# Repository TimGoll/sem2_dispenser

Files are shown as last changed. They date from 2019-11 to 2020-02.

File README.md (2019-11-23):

# SEM2 Projekt - Vitamintablettenspender

## Teil 1 - Konzeptionierung

- **Produktplanung**
    - [ ] Marktanalysen
    - [ ] Wettbewerbsanalysen
    - [ ] Thenologieanalyse
    - [x] Patenanalyse

- **Projektplan**
    - [ ] Aufgaben
    - [ ] Dauer, Beginn und Ende der Aufgaben
    - [ ] Abhängigkeiten zwischen Aufgaben
    - [ ] ggf. kritischer Pfad

- **Anforderungsliste**
    - [ ] Anforderungen des Lastenheftes präzisier sowei um sinnvolle Anforderungen und Angaben inkl. Verweis auf Lage im Kano-Diagramm ärgenzt (min 20)
    - [ ] Konsistenzmatrix für mindestens 10 Hauptanforderungen

- **Funktionsstruktur**
    - [ ] Allgemeine kybernetische Black-Box-Darstellung
    - [ ] Hierarchische Funktionsstruktur (mindestens 10 Teilfunktionen)
    - [ ] Funktionsmodell mit Darstellung der (mindestens 10) wichtigsten Funktionen

- **Lösungsprinzipien**
    - [ ] Morphologischer Kasten mit (jeweils mindestens 4) Taillösungsprinzipien (ggf. durch geeignte Lösungsfindungsmethoden) für diese wichtigsten Funktionen
    - [ ] Verträglichkeitsmatrix für die Teilprinzipien
    - [ ] Kennzeichnung von mindestens 3 möglichen Gesamtlösungskombinationen im morphologischen Kasten
    - [ ] Bewertung dieser Gesamtlösungskombination

- **Grobentwurf / technische Prinzipskizze**
    - [ ] Anfertigung einer technischen Prinzipskizze zur Verdeutlichung des Wirkprinzips

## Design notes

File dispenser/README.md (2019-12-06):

# Dispenser Software

## Needed Libraries

1. Adafruit SSD1306
2. Adafruit GFX
3. Adafruit RTClib

## Software

### Registering Button Callbacks

Button callbacks are a neat system to easily design the software to do actions on the press of a button. Since no memberfunctions of a class can be passed as an callable callback pointer, the function has to be static. The class reference is then passed as an argument.

```cpp
this->buttonHandler->addCallback(10, RISING, &callbackTest, this);
```

The above shown example registers a callback function `callbackTest` and also passes the parent scope with `this`. Therefore all functions and variables of the class can be used in the callback.

```cpp
static void Main::callbackTest(Main* self, uint8_t type) {
    // code here
}
```

This shows the structure of the callback function. The `self` parameter has to be the type of the class itself and can be used inthe same way as `this` is normally used. The type is specific to this button callback and defines the type of the button event (RISING, FALLING, HIGH).

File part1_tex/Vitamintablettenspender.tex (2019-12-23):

%Dokumentklasse
\documentclass[a4paper,12pt, headings=small, bibtotoc, numbers=noenddot]{scrreprt} %bibtotoc = bibliography to table of contents, bindet Literaturverzeichnis in Inhaltsverzeichnis ein
\usepackage[left= 2.5cm,right = 2cm, top = 2cm, bottom = 2cm]{geometry} %Seitenränder
\usepackage[onehalfspacing]{setspace} %1,5 Zeilenabstand

% ============= Packages =============

% Dokumentinformationen
\usepackage[
	pdftitle={Titel der Arbeit},
	pdfsubject={Abschlussarbeit},
	pdfauthor={Max Mustermann},
	pdfkeywords={}
	pdftex=true, 
	colorlinks=true,
 	breaklinks=true,
	citecolor=black,
	linkcolor=black,	
	menucolor=black,	
	urlcolor=black,
]{hyperref}

% Standard Packages
\usepackage{libertine}	%Schriftart "Biolinum", Sans Serif
\renewcommand*\familydefault{\sfdefault} %Setzt die Standardschriftart auf Sans Serif
\usepackage[T1]{fontenc}
\usepackage{mathptmx} %Times new roman
\usepackage[utf8]{inputenc}
\usepackage[ngerman]{babel}
\AtBeginDocument{\renewcommand{\chaptername}{}}

\usepackage{rotating}
\usepackage{subfigure}
\usepackage{graphicx}
\graphicspath{{img/}}

\usepackage{multirow}
\usepackage{placeins}

\usepackage{fancyhdr}
\usepackage{lmodern}
\usepackage{color}
\usepackage{transparent}
\usepackage[justification=centering, singlelinecheck=false]{caption} %Damit die Tabellenbeschriftung zentriert steht
\usepackage{nomencl}
\usepackage{tabularx}
\usepackage{longtable}
\usepackage{booktabs}
\usepackage{pdfpages}
\usepackage{acronym}
\usepackage{setspace}

%Schriftgröße von section auf 12pt setzen
\addtokomafont{section}{\normalsize} 
\addtokomafont{chapter}{\large}
%Abbildungsbeschriftungen fett gedruckt einstellen
\addtokomafont{captionlabel}{\bfseries}

%Abstände zwischen Text und Überschriften
%Zeilenabstände bei Unterkapiteln
\RedeclareSectionCommand[beforeskip=18pt, afterskip=6pt]{section}
%Zeilenabstände bei Unter-unterkapiteln 
\RedeclareSectionCommand[beforeskip=12pt,afterskip=1pt]{subsection}
\RedeclareSectionCommand[%
  beforeskip=0pt,
  afterskip=1\baselineskip plus .1\baselineskip minus .167\baselineskip
]{chapter}

% zusätzliche Schriftzeichen der American Mathematical Society
\usepackage{amsfonts}
\usepackage{amsmath}

\usepackage{float} %erlaubt die Verwendung von H in Bildern
% mu im normalen Text: \textmu
\usepackage{textcomp}

\usepackage[backend=bibtex, style=alphabetic, uniquename=allfull, minalphanames=4, maxalphanames=4]{biblatex}
\addbibresource{Literatur.bib}

% nicht einrücken nach Absatz
\setlength{\parindent}{0pt}

\setcounter{secnumdepth}{4}
\setcounter{tocdepth}{4}

%url umbrechen
\usepackage{url}
\usepackage{microtype} %Sorgt für bessere Platzausnutzung der \hbox bei Umbruechen
\setlength{\emergencystretch}{1em} %Sorgt für bessere Platzausnutzung der \hbox bei Umbruechen

\setcounter{biburlnumpenalty}{100}
\setcounter{biburlucpenalty}{100}
\setcounter{biburllcpenalty}{100}
% ============= Package Einstellungen & Sonstiges ============= 

%römische Aufzählungen mit \RM{Zahl}
\newcommand{\RM}[1]{\MakeUppercase{\romannumeral #1}}

% ============= Dokumentbeginn =============

\begin{document}

\pagestyle{empty}   %leere Seite

%Seitennummerierung neu beginnen, Zahlen [arabic], röm.Zahlen [roman,Roman], Buchstaben [alph,Alph]

%Deckblatt
\label{Coversheet}
\begin{minipage}{0.5\textwidth}
\begin{flushleft}
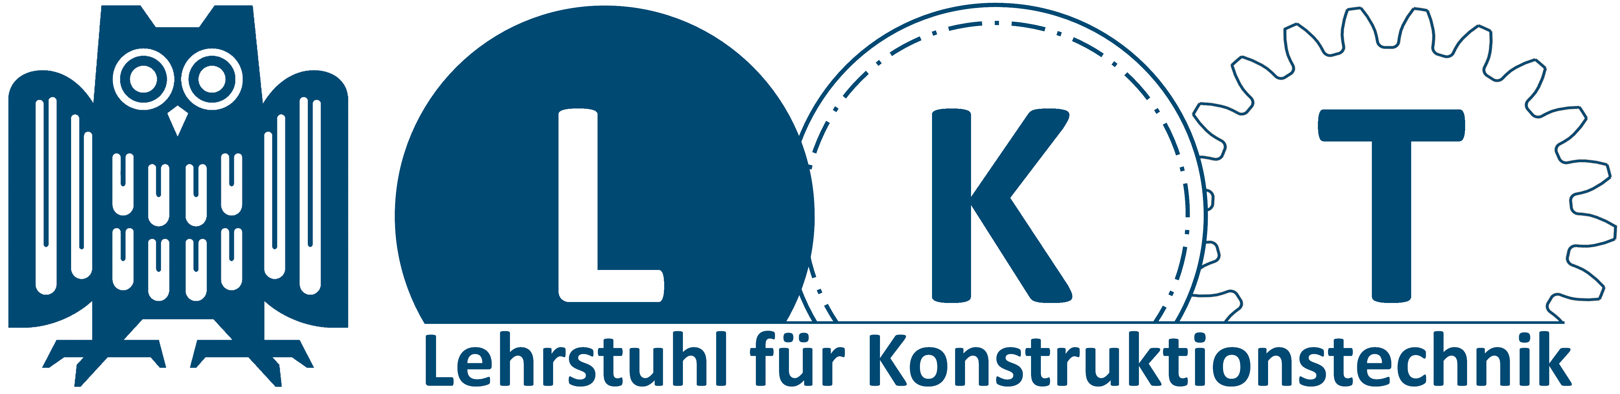
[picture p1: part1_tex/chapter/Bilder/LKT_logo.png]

\end{flushleft}
\end{minipage}
\begin{minipage}{0.5\textwidth}
\begin{flushright}
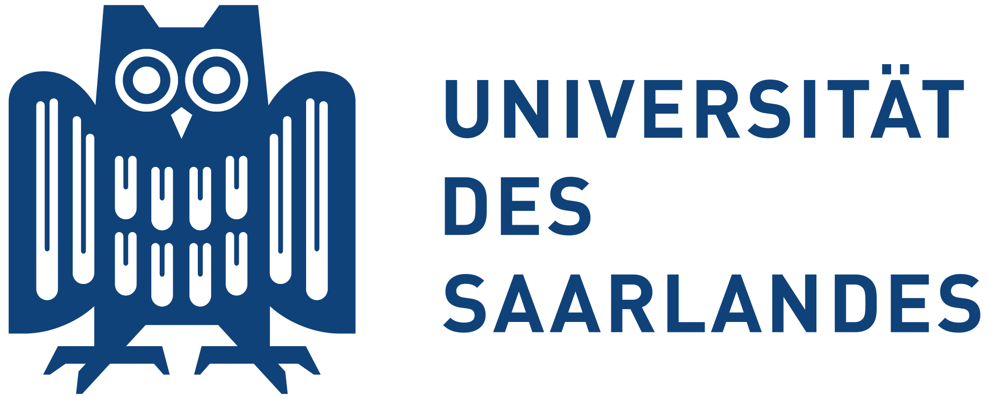
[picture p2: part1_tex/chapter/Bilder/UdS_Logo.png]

\end{flushright}
\end{minipage}
\headrule

\vspace{1.5cm}

\begin{center}
\LARGE \textbf{Vitamintablettenspender}\\ 
\vspace{3cm}
\textbf{Projektarbeit} \\
\Large Systementwicklungsmethodik 2\\ 
WS 2019/20\\
im Studiengang Systems Engineering\\
der Naturwissenschaftlich-Technischen Fakultät \\
der Universität des Saarlandes\\
\vspace{2.5cm}
\Large von\\
\vspace{1cm}
Kristian König und Tim Goll\\
Matrikelnummern: 2560270, 2553050 \\
Gruppennummer: 1\\
\vspace{1cm}
Saarbrücken, 2020
\end{center}
\newpage 

%Leerseite für doppelseitigen Druck
\thispagestyle{empty}
\quad 
\newpage

%Aufgabenstellung
%Hier wird die der verfassten Arbeit zugehörige Aufgabenstellung im PDF-Format eingebunden. Dazu wird im folgenden Block der Titel ,,Aufgabenstellung.pdf'' durch den entsprechenden Dateinamen ersetzt.
\label{Aufgabenstellung}
\includepdf[pages={1-5}]{chapter/Bilder/aufgabenstellung} 
\newpage

%Leerseite für doppelseitigen Druck
%\thispagestyle{empty}
%\quad 
%\newpage

%Eidestatliche Erklärung
%\label{Erklaerung}

%\begin{center} 
%\begin{minipage}[t]{120mm}
% \vspace{8cm}
%Ich versichere hiermit, dass ich die vorliegende Arbeit
%angegebenen Quellen und Hilfsmittel benutzt habe.\\  
%\end{minipage}
%\end{center}

%\vspace{3cm}
%Saarbrücken, den 30.04.2018  ~~~~~~~~~~~~~~~~~~~~~~~~~~~~~~~~~~~~~~~~~~~~~~~ Vorname Nachname
%\newpage

%Leerseite für doppelseitigen Druck
%\thispagestyle{empty}
%\quad 
%\newpage

\pagestyle{fancy} \newpage   %Seitenlayout normal
\fancyhf{} 
\fancyhead[L]{\nouppercase{{\fancyplain{}{\rightmark }}} } 
\fancyhead[R]{\thepage} 
\renewcommand{\headrulewidth}{0.5pt} 
\pagenumbering{Roman}

%Inhaltsverzeichnis
\clearpage \thispagestyle{empty}  ~ \clearpage \tableofcontents \thispagestyle{empty} \newpage

%Seitennummerierung neu beginnen, Zahlen [arabic], röm.Zahlen [roman,Roman], Buchstaben [alph,Alph]
\pagenumbering{arabic} \newpage
\renewcommand*{\chapterpagestyle}{empty}

%Einbinden aller .tex-Dateien, welche die einzelnen Kapitel beinhalten
\include{chapter/01_Lastenheft}
\include{chapter/02_Konzeptionierung}
\include{chapter/03_Detaillierung}
%\include{chapter/04_Ausarbeitung}
%\include{chapter/05_Prototypenbau}

%Abbildungsverzeichnis
\listoffigures \thispagestyle{empty} \newpage

%Tabellenverzeichnis
\listoftables \thispagestyle{empty} \newpage

\printbibliography

%Einbinden des Anhangs
\appendix
\include{chapter/A_Anhang}

\end{document}

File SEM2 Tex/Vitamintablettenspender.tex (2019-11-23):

%Dokumentklasse
\documentclass[a4paper,12pt, headings=small, bibtotoc, numbers=noenddot]{scrreprt} %bibtotoc = bibliography to table of contents, bindet Literaturverzeichnis in Inhaltsverzeichnis ein
\usepackage[left= 2.5cm,right = 2cm, top = 2cm, bottom = 2cm]{geometry} %Seitenränder
\usepackage[onehalfspacing]{setspace} %1,5 Zeilenabstand

% ============= Packages =============

% Dokumentinformationen
\usepackage[
	pdftitle={Titel der Arbeit},
	pdfsubject={Abschlussarbeit},
	pdfauthor={Max Mustermann},
	pdfkeywords={}
	pdftex=true, 
	colorlinks=true,
 	breaklinks=true,
	citecolor=black,
	linkcolor=black,	
	menucolor=black,	
	urlcolor=black,
]{hyperref}

% Standard Packages
\usepackage{libertine}	%Schriftart "Biolinum", Sans Serif
\renewcommand*\familydefault{\sfdefault} %Setzt die Standardschriftart auf Sans Serif
\usepackage[T1]{fontenc}
\usepackage{mathptmx} %Times new roman
\usepackage[utf8]{inputenc}
\usepackage[ngerman]{babel}
\AtBeginDocument{\renewcommand{\chaptername}{}}

\usepackage{rotating}
\usepackage{subfigure}
\usepackage{graphicx}
\graphicspath{{img/}}

\usepackage{multirow}

\usepackage{fancyhdr}
\usepackage{lmodern}
\usepackage{color}
\usepackage{transparent}
\usepackage[justification=centering, singlelinecheck=false]{caption} %Damit die Tabellenbeschriftung zentriert steht
\usepackage{nomencl}
\usepackage{tabularx}
\usepackage{longtable}
\usepackage{booktabs}
\usepackage{pdfpages}
\usepackage{acronym}
\usepackage{setspace}

%Schriftgröße von section auf 12pt setzen
\addtokomafont{section}{\normalsize} 
\addtokomafont{chapter}{\large}
%Abbildungsbeschriftungen fett gedruckt einstellen
\addtokomafont{captionlabel}{\bfseries}

%Abstände zwischen Text und Überschriften
%Zeilenabstände bei Unterkapiteln
\RedeclareSectionCommand[beforeskip=18pt, afterskip=6pt]{section}
%Zeilenabstände bei Unter-unterkapiteln 
\RedeclareSectionCommand[beforeskip=12pt,afterskip=1pt]{subsection}
\RedeclareSectionCommand[%
  beforeskip=0pt,
  afterskip=1\baselineskip plus .1\baselineskip minus .167\baselineskip
]{chapter}

% zusätzliche Schriftzeichen der American Mathematical Society
\usepackage{amsfonts}
\usepackage{amsmath}

\usepackage{float} %erlaubt die Verwendung von H in Bildern
% mu im normalen Text: \textmu
\usepackage{textcomp}

\usepackage[backend=biber, style=alphabetic,uniquename=allfull,minalphanames=4,maxalphanames=4]{biblatex}
\addbibresource{Literatur.bib}

% nicht einrücken nach Absatz
\setlength{\parindent}{0pt}

\setcounter{secnumdepth}{4}
\setcounter{tocdepth}{4}

%url umbrechen
\usepackage{url}

\usepackage{microtype} %Sorgt für bessere Platzausnutzung der \hbox bei Umbruechen
\setlength{\emergencystretch}{1em} %Sorgt für bessere Platzausnutzung der \hbox bei Umbruechen

\setcounter{biburlnumpenalty}{100}
\setcounter{biburlucpenalty}{100}
\setcounter{biburllcpenalty}{100}
% ============= Package Einstellungen & Sonstiges ============= 

%römische Aufzählungen mit \RM{Zahl}
\newcommand{\RM}[1]{\MakeUppercase{\romannumeral #1}}

% ============= Dokumentbeginn =============

\begin{document}

\pagestyle{empty}   %leere Seite

%Seitennummerierung neu beginnen, Zahlen [arabic], röm.Zahlen [roman,Roman], Buchstaben [alph,Alph]

%Deckblatt
\label{Coversheet}
\begin{minipage}{0.5\textwidth}
\begin{flushleft}

\end{flushleft}
\end{minipage}
\begin{minipage}{0.5\textwidth}
\begin{flushright}

\end{flushright}
\end{minipage}
\headrule

\vspace{1.5cm}

\begin{center}
\LARGE \textbf{Vitamintablettenspender}\\ 
\vspace{3cm}
\textbf{Projektarbeit} \\
\Large Systementwicklungsmethodik 2\\ 
WS 2019/20\\
im Studiengang Systems Engineering\\
der Naturwissenschaftlich-Technischen Fakultät \\
der Universität des Saarlandes\\
\vspace{2.5cm}
\Large von\\
\vspace{1cm}
Kristian König und Tim Goll\\
Matrikelnummern: 2560270, 1234567 \\
Gruppennummer: 1\\
\vspace{1cm}
Saarbrücken, 2019
\end{center}
\newpage 

%Leerseite für doppelseitigen Druck
\thispagestyle{empty}
\quad 
\newpage

%Aufgabenstellung
%Hier wird die der verfassten Arbeit zugehörige Aufgabenstellung im PDF-Format eingebunden. Dazu wird im folgenden Block der Titel ,,Aufgabenstellung.pdf'' durch den entsprechenden Dateinamen ersetzt.
\label{Aufgabenstellung}
\includepdf[pages={1-5}]{Bilder/aufgabenstellung}
\newpage

%Leerseite für doppelseitigen Druck
%\thispagestyle{empty}
%\quad 
%\newpage

%Eidestatliche Erklärung
%\label{Erklaerung}

%\begin{center} 
%\begin{minipage}[t]{120mm}
% \vspace{8cm}
%Ich versichere hiermit, dass ich die vorliegende Arbeit
%angegebenen Quellen und Hilfsmittel benutzt habe.\\  
%\end{minipage}
%\end{center}

%\vspace{3cm}
%Saarbrücken, den 30.04.2018  ~~~~~~~~~~~~~~~~~~~~~~~~~~~~~~~~~~~~~~~~~~~~~~~ Vorname Nachname
%\newpage

%Leerseite für doppelseitigen Druck
%\thispagestyle{empty}
%\quad 
%\newpage

\pagestyle{fancy} \newpage   %Seitenlayout normal
\fancyhf{} 
\fancyhead[L]{\nouppercase{{\fancyplain{}{\rightmark }}} } 
\fancyhead[R]{\thepage} 
\renewcommand{\headrulewidth}{0.5pt} 
\pagenumbering{Roman}

%Inhaltsverzeichnis
\tableofcontents \thispagestyle{empty} \newpage

%Abbildungsverzeichnis
\listoffigures \thispagestyle{empty} \newpage

%Tabellenverzeichnis
\listoftables \thispagestyle{empty} \newpage

%Seitennummerierung neu beginnen, Zahlen [arabic], röm.Zahlen [roman,Roman], Buchstaben [alph,Alph]
\pagenumbering{arabic} \newpage
\renewcommand*{\chapterpagestyle}{empty}

%Einbinden aller .tex-Dateien, welche die einzelnen Kapitel beinhalten
\include{01_Lastenheft}
\include{02_Konzeptionierung}
\include{03_Detaillierung}
\include{04_Ausarbeitung}
\include{05_Prototypenbau}

\printbibliography

%Einbinden des Anhangs
\appendix
\include{A_Anhang}

\end{document}

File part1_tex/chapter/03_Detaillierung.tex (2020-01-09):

% !TeX encoding = UTF-8
% !TeX root = ../Vitamintablettenspender.tex

\chapter{Methodische Werkstoffauswahl}
Von der Produktentwicklung werden leistungsfähige Systeme bei gleichzeitiger Erfüllung von Sicherheits- und Umweltverträglichkeitsanforderungen erwartet. Steigenden Kosten für Material und Energie werden im Zuge des Multi-Material-Designs mittels einer methodischen Werkstoffauswahl durch die \glqq Ashby-Methode\glqq{} und den dabei entstehenden intelligenten Lösungen entgegengewirkt. Dabei werden unterschiedlichste Aspekte wie die Möglichkeit zur generativen Fertigung bzw. dem Additive Manufacturing berücksichtigt. Die Auslegung der Hauptkomponenten des Produktes unterliegt den jeweils gültigen Randbedingungen und ihren zu erfüllenden Funktionen und werden hinsichtlich ihrer freien Variablen untersucht und bezüglich der Werkstoffauswahl optimiert. Eine \glqq Performance-Rechnung\grqq{} ermöglicht die Einbeziehung von mathematischen und physikalischen Formeln zur Entmystifizierung der Werkstofffaktoren. In der kommerziellen Software CES Selector der Firma Granta Design Ltd. (Cambridge, Vereinigtes Königreich), die von Michael Ashby, dem Erfinder der Ashby-Methode, gegründet wurde, wird mittels einer computergestützten Datenbank auf Basis der Performance-Rechnung die fünf besten in Frage kommenden Werkstofflösungen mit ihren Materialindizees ermittelt, woraus die optimale Werkstofflösung durch \glqq weiche\grqq{} Faktoren und den Prozesstechnologien resultiert.\\
Für die Anwendung der Ashby-Methode muss zunächst die Hauptfunktion des Bauteils bestimmt werden. Darauffolgend müssen Randbedingungen definiert werden, auf Basis derer ein Ziel zur Optimierung gesetzt wird. Dabei treten freie Variablen auf, die während des Designprozesses des Produktes variiert werden können. Die Randbedingungen liefern im Allgemeinen numerische Gleichungen die einen Performance-Index implizieren. Ein höherer Performance-Index bedeutet konventionell ein besseres Material.\\
Im Folgenden wird das Prinzip von Ashby zur Materialauswahl auf die vier Hauptkomponenten des Systems angewandt. Dabei handelt es sich zunächst um das Gehäuse, worin der Standfuß, die Rückwand sowie die Oberseite zusammengefasst werden. Ein weiteres Bauteil, das der Werkstoffoptimierung unterzogen wird, ist die Tablettenrutsche, an die die ausgeworfenen Tabletten übergeben und zum Trinkbehälter transportiert werden. Dritte Hauptkomponente stellt die rohrförmige, transparente Tablettenlagerung. Zum Schluss werden die Aktoren, welche sich aus Pleuelstangen und einem Tablettenschieber zusammensetzen untersucht.

\section{Standfuß und Gehäuse}\label{section:3.1}
Das Gehäuse inklusive des Standfußes sowie der Oberseite zum Anschrauben der übrigen Bauteile ist im Querschnitt zusammen mit den wesentlich angreifenden Lasten in Abb. 3.1(a) dargestellt. Die Streckenlast $q_0$ fasst die Gewichtskräfte der Tablettenrutsche, der Aktoren sowie der Behälter für die Lagerung der Tabletten zusammen. Die Einspannung am unteren Ende symbolisiert die Lagerung des Bauteils an der Oberfläche. Eine geeignete Vereinfachung wird in Abb. 3.1(b) beschrieben. Darin ist die Kraft $F_{res}$ die Resultierende aus der Streckenlast und greift im Schwerpunkt der Last an. Die Einspannung am unteren Ende reduziert sich zu der für die Berechnung wesentlichen vertikalen Komponente $F_{L,V}$. Unter Vernachlässigung des Eigengewichts des Bauteils gilt näherungsweise $F_{res}\,\approx\,F_{L,V}$. Die Werkstoffauswahl und die Optimierung einer Zielfunktion kann für den dargestellten kritischen Teil des Gehäuse stellvertretend für die gesamte Struktur vorgenommen werden.
\begin{figure}[H]
	\centering
	\subfigure[Querschnitt des Gehäuses und angreifende Lasten]{}\label{fig:0301skizzea}
	\qquad
	\subfigure[Vereinfachte Darstellung mit angreifenden, resultierenden Kräften und der kritischen Zone]{\label{fig_0301skizzeb}}\label{fig:0301skizzeb}
	\caption{Schematische Darstellung des Gehäuses}
\end{figure}
\begin{figure}[H]
	\centering
	
	\caption{Abstrahiertes Modell einer Platte unter reiner Biegung mit dem Biegemoment~$M_b$}
	\label{fig:0301model}
\end{figure}
Dabei ist die \textbf{Funktion} des Bauteils die Tablettenrutsche, die Aktoren sowie die Tablettenbehälter zu stützen und in der Höhe zu halten. Auf Basis der Anforderungsliste in \ref{anforderungsliste} und der benötigten mechanischen Eigenschaften können folgende \textbf{Randbedingungen} definiert werden:
\begin{itemize}
	\item Material muss recyclebar sein
	\item Material muss ein guter Isolator sein, bzw. $\rho_e\,>\,10^{19}\,\mu\Omega$cm
	\item CO$_2$-Ausstoß bei der Materialgewinnung $\le\,2\,\frac{\text{kg}\,(\text{CO}_2)}{\text{kg}\,(\text{Material})}$
	\item Spezifische Festigkeit $\ge\,5\,\frac{\text{kN}\,\text{m}}{\text{kg}}$
	\item Bruchzähigkeit $\ge\,1\,\text{MPa}\,\sqrt{\text{m}}$
	\item Höhe des kritischen Teils/Länge der Platte $L\,=\,180\,$mm
	\item Biegesteifigkeit $S$ so, dass bei Einleitung der Kraft $F_{res}$ das an der Platte resultierende Biegemoment $M_b$ eine maximale Durchbiegung $w_{\text{max}}$ zur Folge hat
\end{itemize}
Das \textbf{Ziel} der Werkstoffauswahl ist die Reduzierung der Kosten für das Gehäuse. Als \textbf{freie Variablen} treten dabei zum einen die Querschnittfläche der rückwandigen Platte, welche durch Konzeptleichtbau im Verlauf des Produktdesigns optimiert werden kann, zum anderen die Wahl des Materials.
Als Grundlage der Performance-Rechnung dient das abstrahierte Model aus \ref{fig:0301model}. Hierbei gilt zunächst für die Durchbiegung in der vertikalen Mitte der Platte ausgehend von der Differentialgleichung 2. Ordnung:
\begin{equation}
	E\,I\,w''(x)\,=\,-\,M_b\,.
\end{equation}
nach zweifachem Integrieren, Umstellen und Einsetzen unter Vernachlässigung des Vorzeichens, das ausschließlich für die Richtung der Durchbiegung berücksichtigt werden muss:
\begin{equation} \label{durchbiegung}
	w\,\left(\frac{L}{2}\right)\,=\,\frac{M_b \,L^2}{8\,E\,I}\,\le\,w_{\text{max}},
\end{equation}
wobei $E\,I$ der Biegesteifigkeit $S$ entspricht. Als weitere Gleichung ergibt sich der Zusammenhang für die effektiven Kosten $K$, die in erster Linie über den Kostenfaktor $C_m$ mit der Masse der Platte korrelieren. Unter Berücksichtigung der Geometrie und der Materialdichte $\rho$ ergibt sich:
\begin{equation} \label{kosten}
	K\,=\,C_m\,m\,=\,C_m\,\rho\,A\,L\,.
\end{equation}
Dabei ist das Flächenträgheitsmoment eine Funktion der Querschnittfläche, die als rechteckig angenähert werden kann. Hier sind jedoch die Kantenlängen $h$ und $b$ variabel. Damit gilt für die Querschnittsfläche:
\begin{equation} \label{flächeninhalt}
A\,=\,h\,b
\end{equation}
sowie für das Flächenträgheitsmoment:
\begin{equation} \label{flächenträgheitsmoment}
I\,=\,\frac{h\,b^3}{12}\,.
\end{equation}
Einsetzen von \ref{flächenträgheitsmoment} in \ref{durchbiegung} und \ref{flächeninhalt} in \ref{kosten} liefert die Gleichungen:
\begin{equation} \label{eingesetzt}
	w_{\text{max}}\,\ge\,\frac{3\,M_b \,L^2}{2\,E\,h\,b^3}\,, \qquad
	K\,=\,C_m\,\rho\,h\,b\,L\,.
\end{equation}
Eliminieren von $b$ führt in \ref{eingesetzt} schließlich zu
\begin{equation}\label{performance}
K\,=\,\underbrace{\left(\frac{3\,M_b\,L^5\,h^3}{2\,w_{\text{max}}}\right)^{\frac{1}{3}}}_{\text{konstanter Vorfaktor}}\,\frac{C_m\,\rho}{E^{\frac{1}{3}}}\,.
\end{equation}
Die \textbf{Zielfunktion} ist damit durch
\begin{equation} \label{performance31}
P_{\text{CR}}^{3.1}\,=\,\frac{1}{K}\,=\,\frac{E^\frac{1}{3}}{C_m\,\rho}
\end{equation}
definiert, wobei der Materialindex $P_{\text{CR}}^{3.1}$ zu maximieren ist. Dabei stellen hohe Werte von $P_{\text{CR}}^{3.1}$ einen idealen Kompromiss aus den Kosten und der Biegesteifigkeit dar.\\
Logarithmieren von \ref{performance31} liefert die Beziehung
\begin{equation}
\underbrace{3\,\ln(P_{\text{CR}}^{3.1})}_{=\,\text{konst.}}\,=\,\ln(E)\,-\,3\,\ln(C_m\,\rho)\,,
\end{equation}
wodurch sich mittels der Ashby-Methode in den Graph des logarithmierten Elastizitäsmodul über dem logarithmierten Produkt aus den Kosten und der Materialdichte eine Designgerade der Steigung 3 legen lässt, welche einen variablen y-Achsenabstand in Abhängigkeit des Materialindex' aufweist, s. Abb. \ref{fig:ces_3_1_1}.\\
\begin{figure}[H]
	\centering
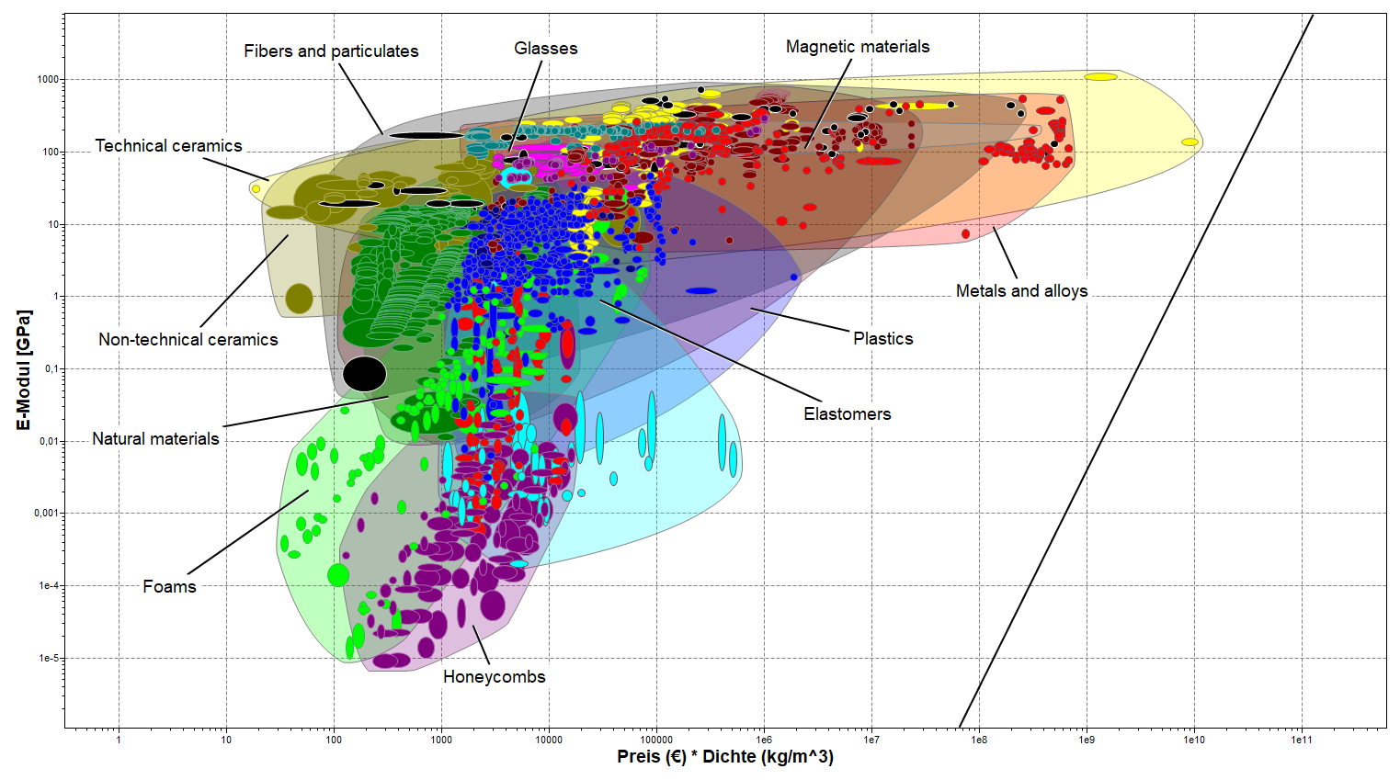
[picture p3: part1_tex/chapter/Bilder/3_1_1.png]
	
	\caption{Eigenschaftsdiagramm für die Werkstoffauswahl des Gehäuses inklusive der Designgeraden mit der Steigung 3}
		\label{fig:ces_3_1_1}
\end{figure}
Hinzufügen der Randbedingungen \glqq recyclebar\grqq{} und \glqq guter Isolator\grqq{} eliminiert einige Materialien und führt zur graphischen Darstellung in Abb. \ref{fig:ces_3_1_2}.\\
\begin{figure}[H]
	\centering
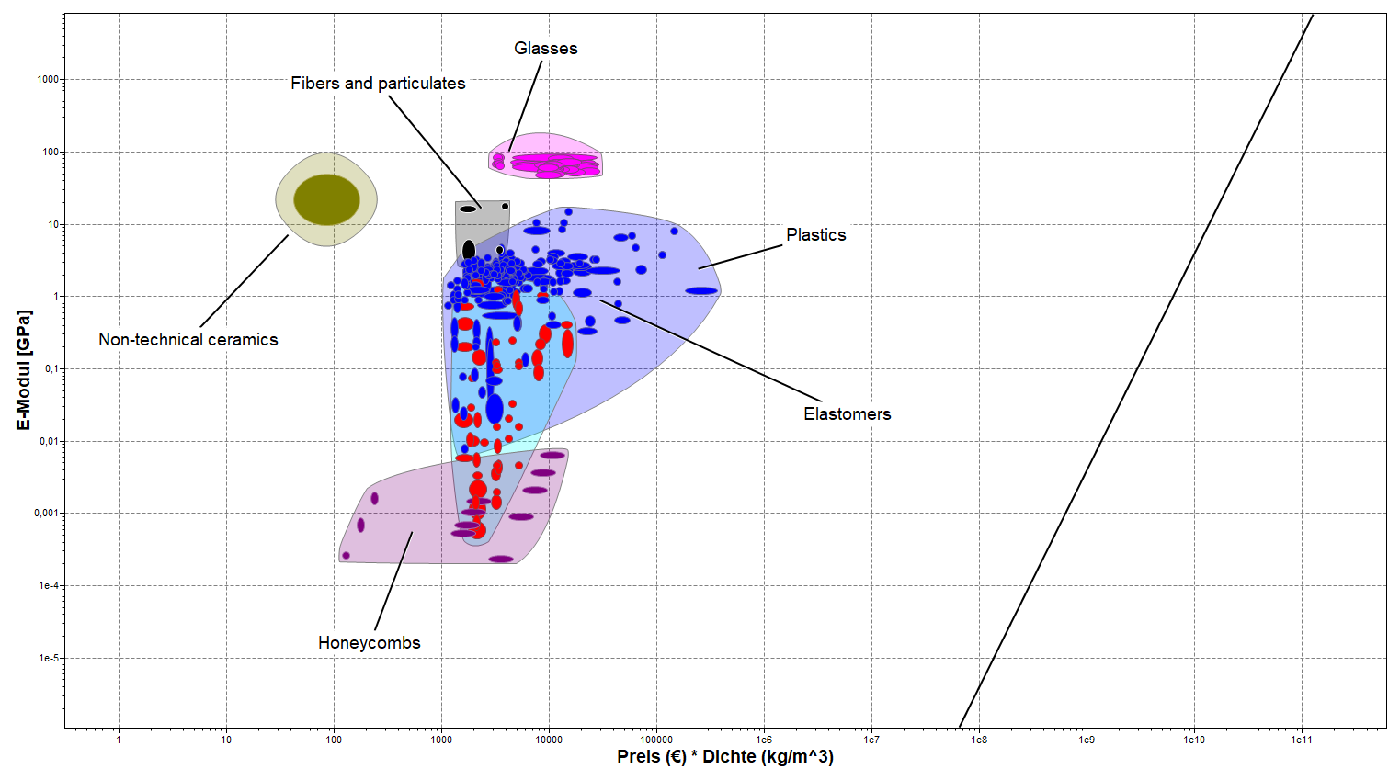
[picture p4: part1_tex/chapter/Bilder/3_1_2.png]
	
	\caption{Eigenschaftsdiagramm für die Wahl des Materials des Gehäuses nach Hinzufügen einiger Randbedingungen}
	\label{fig:ces_3_1_2}
\end{figure}
Unter Berücksichtigung der übrigen Randbedingungen hinsichtlich des CO$_2$-Ausstoßes und der mechanischen Materialeigenschaften scheiden weitere Materialien aus (Abb. \ref{fig:ces_3_1_3}).\\
\begin{figure}[H]
	\centering
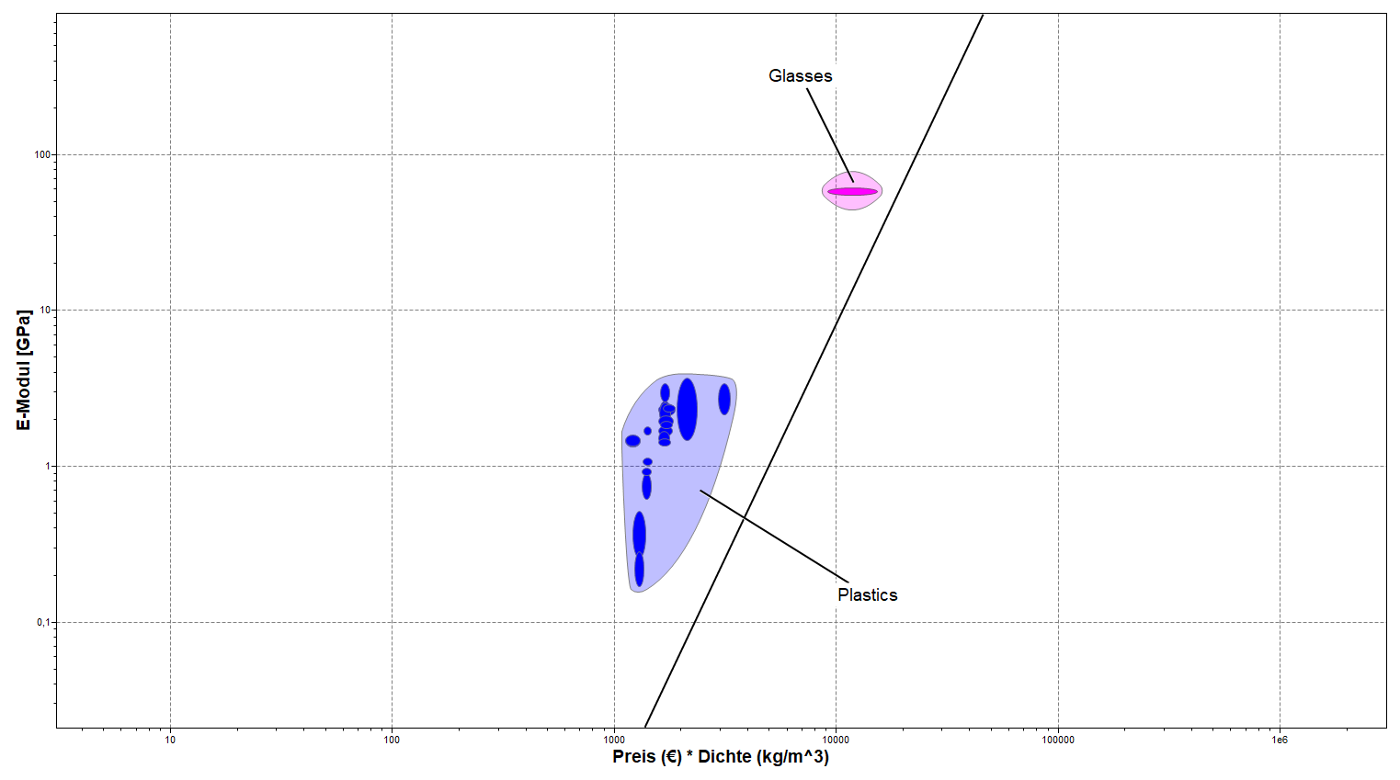
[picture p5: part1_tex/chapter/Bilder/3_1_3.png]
	
	\caption{Eigenschaftsdiagramm aller möglicher Materialien unter Berücksichtigung der Randbedingungen mit leicht verschobener Designgerade}
	\label{fig:ces_3_1_3}
\end{figure}
Erhöhung des y-Achsenabschnittes der Gerade führt zur Vernachlässigung aller Materialien, die unterhalb der Geraden liegen. Das am besten geeignete Material wird zuletzt von der Gerade eliminiert und weist den höchsten Performance-Index $P_{\text{CR}}^{3.1}$ auf (Abb. \ref{fig:ces_3_1_4}).\\
\begin{figure}[H]
	\centering
	
	\caption{Top 5 Materialien für das Gehäuse nach der Ashby-Methode}
	\label{fig:ces_3_1_4}
\end{figure}
Die fünf geeignetsten Materialien werden dadurch ausfindig gemacht, dass sie zuletzt von der Gerade eliminiert werden und damit den höchsten Performance-Index besitzen. Für das betrachtete Problem ergibt sich:
\begin{itemize}
\item[1)] Polypropylen (PP, Materialindex: 9,46$\,\times10^{-4}$)
\item[2)] Polyethylen (PE, HD - high density, 7,3$\,\times10^{-4}$)
\item[3)] Polyethylen (PE, LD - low density, 5,55$\,\times10^{-4}$)
\item[4)] Polyvinylchlorid (PVC, 4,48$\,\times10^{-4}$)
\item[5)] Natron- und kaligeschmelztes Glas (3,3$\,\times10^{-4}$)
\end{itemize}
Polypropylen ist ein sehr gut zu verarbeitendes Material. Es lässt sich Spritzgießen, Extrudieren oder auch Tiefziehen. Aufgrund der vielfältigen Möglichkeiten zur Produktion des Bauteils aus Polypropylen, wobei Spritzgießen bevorzugt wird, fällt ohne weitere Einschränkung oder offensichtliche Nachteile die Wahl des Materials für das Gehäuse auf Polypropylen. Es stellt einen idealen Kompromiss aus Dichte, Preis und Elastizitätsmodul dar.

\section{Tablettenrutsche}
Die Tablettenrutsche besitzt die wesentliche \textbf{Funktion} die aus der Lagerung geschobenen Vitamintabletten mittels Schwerkraft entlang einer Bahn in einen bereitgestellten Trinkbehälter zu überführen. Sie wird direkt an das Gehäuse geschraubt und an ihr sind mehrere elektronische Bauteile wie u.a. Taster und die Servomotoren befestigt, daher erfährt hier die elektrische Resistivität eine erhöhte Bedeutung. Für die Werkstoffauswahl liegen insgesamt folgenden \textbf{Randbedingungen} vor:
\begin{itemize}
	\item Material muss recyclebar sein
	\item Material muss generativ bzw. additiv fertigbar sein
	\item Material muss ein guter Isolator sein, bzw. $\rho_e\,>\,10^{19}\,\mu\Omega$cm
	\item Plattengeometrie: Trapezförmiger Querschnitt (gleichschenklig und symmetrisch, Höhe $h\,=\,40\,$mm, Dicke $3\,=\,$mm)
\end{itemize}
Das \textbf{Ziel} der Werkstoffwahl liegt in der Minimierung des CO$_2$-Ausstoßes bei der Materialgewinnung unter Erfüllung der minimalen spezifischen Bruchfestigkeit, die gewährleistet, dass trotz der hohen Zahl an Auswurfzyklen der Tabletten und dem dabei wirkenden Biegemoment die Bauteilstruktur nicht beeinflusst wird und keine Risse an der Oberfläche auftreten. \textbf{Freie Variable} ist in dem Auslegungsprozess die Wahl des Materials sowie die Längen $l_1$ und $l_2$ der beiden Grundseiten der Trapezquerschnittsfläche.\\
\begin{figure}[H]
	\centering
	\subfigure[Draufsicht auf die Tablettenrutsche]{}
	\qquad
	\subfigure[Seitenansicht auf die Tablettenrutsche]{}
	\caption{Die Tablettenrutsche mit Maßen und wirkenden Kräften}
	\label{fig:3_3}
\end{figure}
Aufgrund der vorgegebenen Plattengeometrie (s. Abb. \ref{fig:3_3}) gilt für den CO$_2$-Ausstoß bei der Materialgewinnung in Abhängigkeit der Masse
\begin{equation}\label{masse32}
\text{CO}_2^{ges}\,=\,\text{CO}_2^F\,m\,=\,\text{CO}_2^F\,\rho\,V\,=\,\text{CO}_2^F\,\rho\,\frac{1}{2}\,(l_1\,+\,l_2)\,h\,d\,.
\end{equation}
Für die Normalspannung in der Randfaser der Platte gilt
\begin{equation}
\sigma\,=\,\frac{M_b}{I}\,z\,.
\end{equation}
Dabei ist $M_b$ das Biegemoment, $I$ das Flächenträgheitsmoment und $z$ der Abstand der Randfaser von der neutralen Faser. Damit an der Oberfläche des Bauteils keine Risse auftreten, darf wie in Abb. \ref{fig:3_4} die Spannung $\sigma$ nicht die Bruchfestigkeit $\sigma_f$ überschreiten
\begin{equation}\label{bruchfestigkeit32}
\sigma\,=\,\frac{M_b}{I}\,z\,\le\,\sigma_f\,.
\end{equation}
\begin{figure}[H]
	\centering
	
	\caption{Potentielle Rissbildung an der Einspannung aufgrund des wirkenden Biegemomentes}
	\label{fig:3_4}
\end{figure}
Es folgt für das Biegemoment aufgrund des in Abb. \ref{fig:3_4} dargestellten Lastfalls
\begin{equation}\label{lastfall32}
M\,=\,F\,\cos(45)\,h=\,F\,\frac{\sqrt{2}}{2}\,h\,.
\end{equation}
Unter Berücksichtigung der Plattengeometrie gilt für den Abstand $z$ der Randfaser zur neutralen Faser
\begin{equation}\label{geometrie32}
z\,=\,\frac{d}{2}\,.
\end{equation}
Das Flächenträgheitsmoment des Querschnittes entspricht im Krafteinleitungspunkt:
\begin{equation}\label{flächen32}
I\,=\,\frac{\frac{1}{2}\,(l_1\,+\,l_2)\,d^3}{12}\,=\frac{(l_1\,+\,l_2)\,d^3}{24}\,.
\end{equation}
Einsetzen von \ref{lastfall32}, \ref{geometrie32} und \ref{flächen32} in \ref{bruchfestigkeit32} liefert
\begin{equation}\label{eingesetzt32}
\sigma_f\,\ge\,\frac{24\,\sqrt{2}\,F}{4\,(l_1\,+l_2)\,d^3}\,h\,d\,=\,\frac{6\,\sqrt{2}\,F\,h}{(l_1\,+\,l_2)d^2}\,.
\end{equation}
Schlussendlich führt Eliminierung der freien Variable $(l_1\,+\,l_2)$ in \ref{masse32} und \ref{eingesetzt32} auf
\begin{equation}
\frac{2\,\text{CO}_2^{ges}}{\text{CO}_2^F\,\rho\,h\,d}\,=\,\frac{6\sqrt{2}\,F\,h}{d^2\,\sigma_f}\,.
\end{equation}
Der gesamte CO$_2$-Ausstoß lässt sich dadurch mit
\begin{equation}
\text{CO}_2^{ges}\,=\,\underbrace{\frac{3\,\sqrt{2}\,F\,h^2}{d}}_{\text{konstanter Vorfaktor}}\,\frac{\text{CO}_2^F\,\rho}{\sigma_f}
\end{equation}
berechnen.
Damit ergibt sich die Performance-Gleichung
\begin{equation} \label{zielfkt32}
P_{\text{CR}}^{3.2}\,=\,\frac{1}{\text{CO}_2^{ges}}\,=\,\frac{\sigma_f}{\text{CO}_2^F\,\rho}\,,
\end{equation}
deren Materialindex $P_{\text{CR}}^{3.2}$ zu maximieren ist.\\
Analog zu der in \ref{section:3.1} beschrieben graphischen Umsetzung mittels der Ashby-Methode lässt sich die logarithmierte spezifische Bruchfestigkeit über dem Logarithmus des Produktes von CO$_2$-Fußabdruck und Materialdichte auftragen.\\
\begin{figure}[H]
	\centering
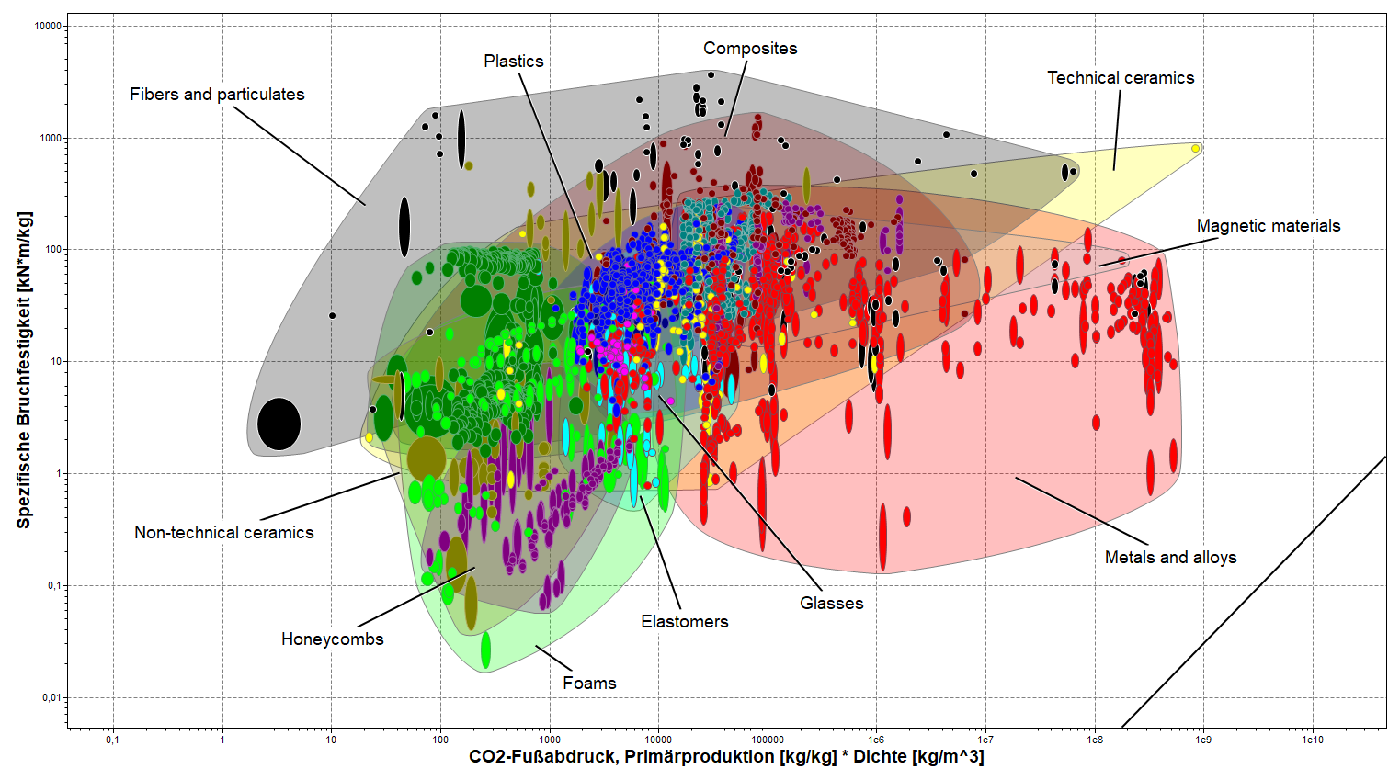
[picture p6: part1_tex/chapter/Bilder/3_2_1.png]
	
	\caption{Eigenschaftsdiagramm für die Werkstoffauswahl die Tablettenrutsche inklusive der Designgeraden mit der Steigung 1}
	\label{fig:ces_3_2_1}
\end{figure}
Hinzufügen aller Randbedingungen eliminiert einige Materialien, s. Abb. \ref{fig:ces_3_2_2}\\
\begin{figure}[H]
	\centering
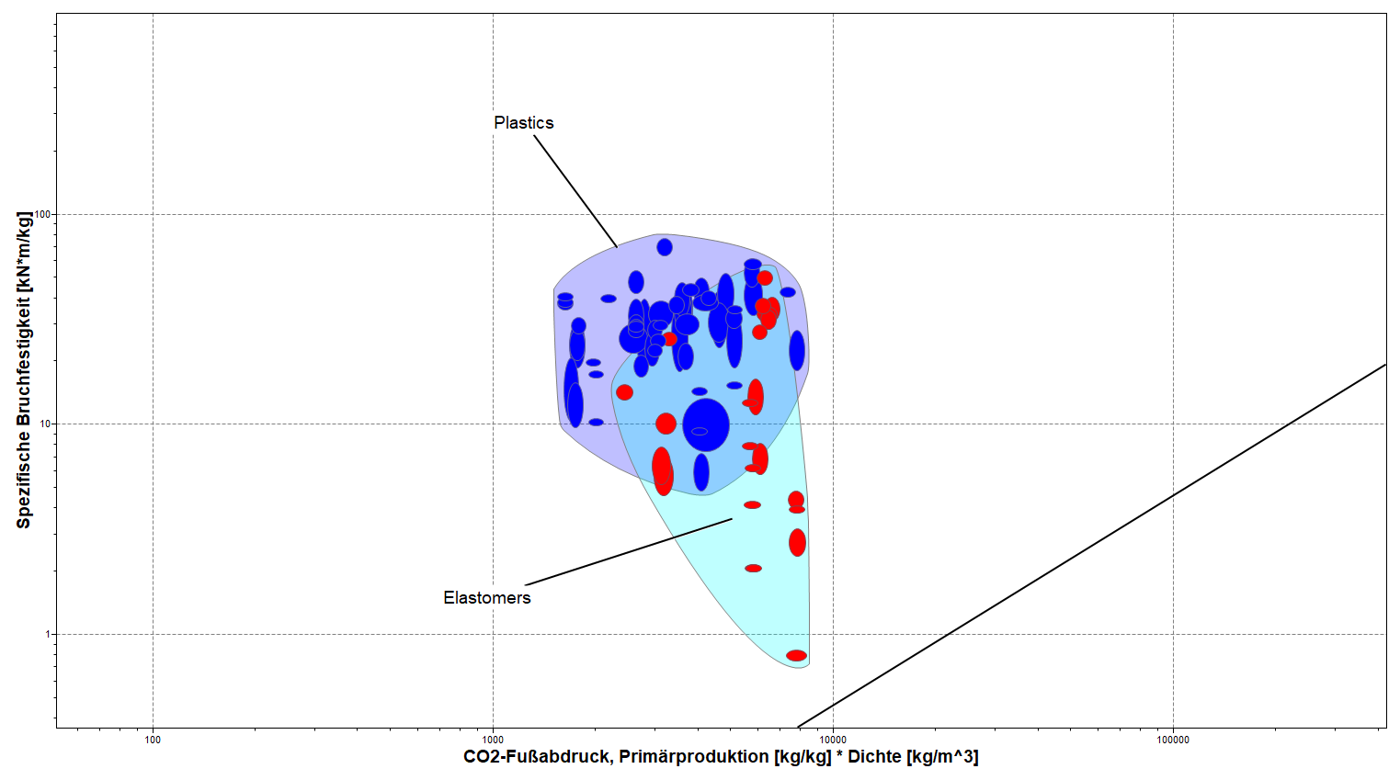
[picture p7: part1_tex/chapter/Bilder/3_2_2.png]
	
	\caption{Eigenschaftsdiagramm aller möglicher Materialien für die Tablettenrutsche unter Berücksichtigung der Randbedingungen mit leicht verschobener Designgerade}
	\label{fig:ces_3_2_2}
\end{figure}
Verschieben der Gerade in positive y-Richtung liefert die am besten geeigneten Materialien. (Abb. \ref{fig:ces_3_2_3})\\
\begin{figure}[H]
	\centering
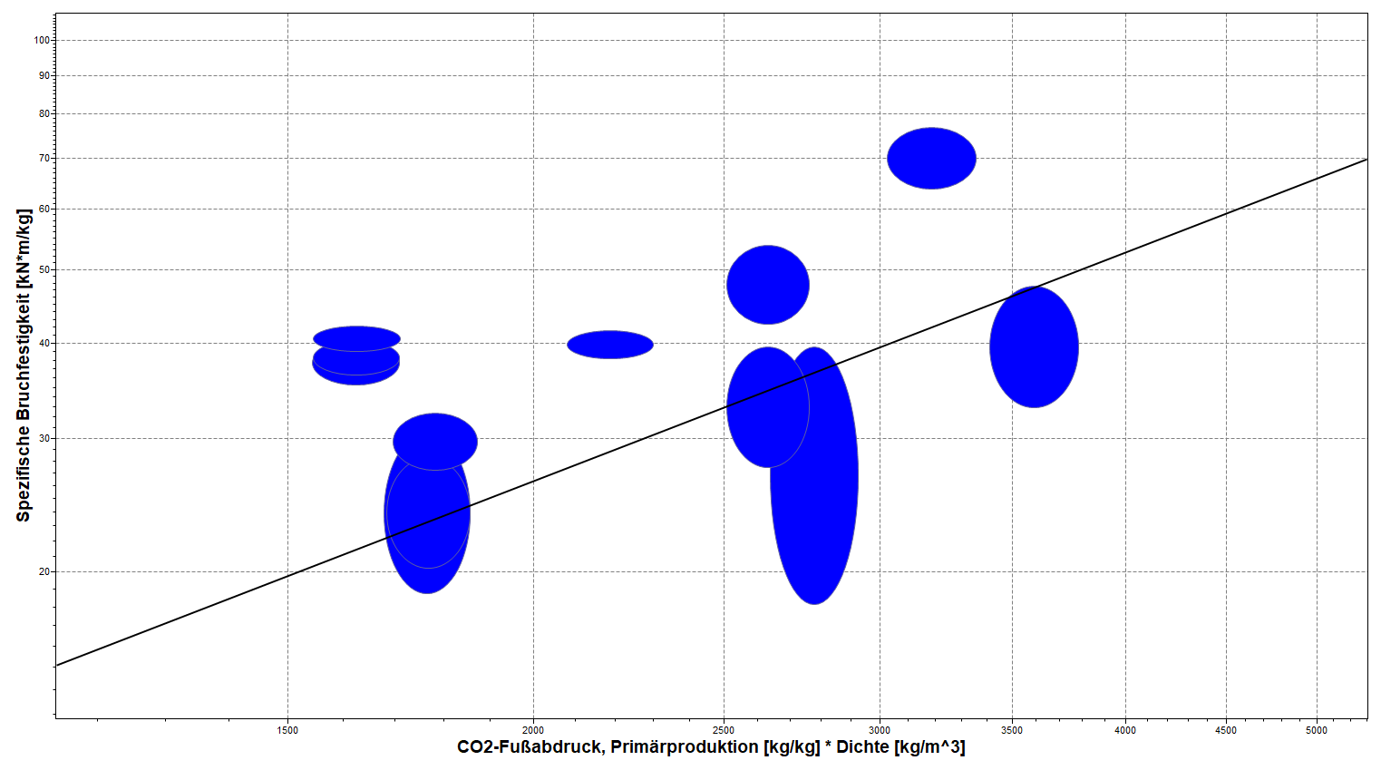
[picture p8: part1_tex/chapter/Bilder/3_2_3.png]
	
	\caption{Top 5 Materialien für die Tablettenrutsche nach der Ashby-Methode}
	\label{fig:ces_3_2_3}
\end{figure}
Die fünf dadurch ausgemachten geeignetsten Materialien lauten:
\begin{itemize}
	\item[1)] Polypropylen (PP, Materialindex: 0,025)
	\item[2)] Styrol-Acrylnitril (SAN, 0,022) 
	\item[3)] Polystyrol (PS, 0,0182)
	\item[4)] Polyethylen (PE, HD - high density, 0,0167)
	\item[5)] Acrylnitril-Butadien-Styrol (ABS, 0,011)
\end{itemize}
Da in \ref{section:3.1} bereits Polypropylen als das bestmögliche Material für das Gehäuse gewählt wurde, fällt die Wahl für die Tablettenrutsche ebenfalls auf PP. Das Material ist sehr gut geeignet für Anwendungen im Lebensmittelbereich, was die Entscheidung stützt. Zudem lässt sich PP sehr gut extrudieren, was ermöglicht, wie vorgegeben die Tablettenrutsche additiv zu fertigen mittels 3D-Druck.

\section{Tablettenlagerung}
Die Tablettenlagerung besteht aus Hohlzylindern, die direkt an die Tablettenrutsche geschraubt werden. Die \textbf{Funktion} dieses Bauteils stellt das sichere Lagern der Vitamintabletten sowie dem Zulassen einer optischen Prüfung des Füllstandes dar. Zur Erfüllung dieser Funktion sind folgende \textbf{Randbedingungen} gegeben:
\begin{itemize}
	\item Material muss recyclebar sein
	\item Material muss durchsichtig/transparent sein
	\item CO$_2$-Ausstoß bei der Materialgewinnung $\le\,2\,\frac{\text{kg}\,(\text{CO}_2)}{\text{kg}\,(\text{Material})}$
	\item Preis $\le\,2\,\frac{\text{€}}{\text{kg}}$
	\item Steifigkeit: Kein Umknicken bei Befüllung
	\item Festigkeit: Keine plastische Verformung bei Befüllung
	\item Bauteilhöhe $l\,=\,200\,$mm
	\item Innenradius des Lagerungsrohrs $r\,=\,14\,$mm
\end{itemize}
Das \textbf{Ziel} der Werkstoffauswahl ist die Minimierung der grauen Energie bei der Materialgewinnung für eine ausreichende Biegesteifigkeit. \textbf{Freie Variable} ist die Wahl des Materials sowie der Außenradius $R$ des Rohrs. Der Belastungszustand unter dem das Bauteil steht, ist in Abbildung ?? dargestellt.
\begin{figure}[H]
	\centering
	\subfigure[Vorderansicht auf den Lagerungszylinder]{}
	\qquad
	\subfigure[Zugehörige Draufsicht]{}
	\caption{Caption TODO}
	\label{fig:3_5}
\end{figure}
Dabei wird das Rohr an der Unterseite fest eingespannt und während des Befüllvorgangs unter Knickung an der Oberkante belastet. Die während der Primärproduktion verbrauchte Energie ist mit
\begin{equation}\label{energie33}
H^{ges}\,=\,H_p\,m\,=\,H_p\,\rho\,l\,A\,=\,H_p\,\rho\,l\,\pi\,\left(R^2\,-\,r^2\right)\,\approx\,c_1\,H_p\,\rho\,l\,\pi\,R^2
\end{equation}
definiert. Da der Innenradius $r$ bekannt ist, kann er näherungsweise durch einen konstanter Vorfaktor in der Rechnung ausgetauscht werden.\\
Da es sich bei dem gegebenen Lastfall, um die Knickung eines Rohres handelt, kann näherungsweise die Theorie des Eulerschen Knickstabes herangezogen werden. Dadurch lässt sich die kritische Last $F_{krit}$, bei der es zum Knick kommt, mit
\begin{equation}\label{fkrit33}
F_{krit}\,=\,\frac{\pi^2\,E\,I}{l^2}\,\ge\,F\,,
\end{equation}
berechnen, wobei die real-angreifende Last $F$ geringer sein muss.
Das Flächenträgheitsmoment für den Rohrquerschnitt ist durch
\begin{equation}\label{flächen33}
I\,=\,\frac{\pi}{4}\,\left(R^4\,-\,r^4\right)\,\approx\,c_2\,\frac{\pi}{4}\,R^4
\end{equation}
definiert. Auch hier geht $r$ nur als Konstante mit ein und kann in einem Produktausdruck durch einen weiteren konstanten Faktor $c_2$ ersetzt werden. Einsetzen von \ref{flächen33} in \ref{fkrit33} liefert
\begin{equation}
F\,\le\,\frac{\pi^2\,E\,c_2\,\frac{\pi}{4}\,R^4}{l^2}\,=\,\frac{c_2\,\pi^3\,E\,R^4}{4\,l^2}\,.
\end{equation}
Eliminieren der freien Variable $R$ führt schließlich im Grenzfall $F\,=\,F_{krit}$ zu
\begin{equation}
F\,=\,\frac{c_2\,\pi^3\,E\,R^4}{4\,l^2}\,=\,\frac{c_2\,\pi^3\,E\,H_{ges}^2}{4\,c_1^2\,l^2\,H_p^2\,\rho^2\,l^2\,\pi}\,=\,\frac{c_2\,\pi\,E\,H_{ges}^2}{4\,c_1^2\,l^3\,\rho^2\,H_p^2}\,.
\end{equation}
Die gesamt aufgewendete Energie in der Produktion lässt sich damit durch
\begin{equation}
H_{ges}\,=\,\underbrace{\left(\frac{4\,c_1^2\,l^3\,F}{c_2\,\pi}\right)^\frac{1}{2}}_{\text{konstanter Vorfaktor}}\,\frac{\rho\,H_p}{E^\frac{1}{2}}
\end{equation}
berechnen.
Es ergibt sich die Performance-Gleichung
\begin{equation} \label{zielfkt3}
P_{\text{CR}}^{3.3}\,=\,\frac{1}{H_{ges}}\,=\,\frac{E^\frac{1}{2}}{H_p\,\rho}\,,
\end{equation}
deren Materialindex $P_{\text{CR}}^{3.3}$ zu maximieren ist. Die graphische Darstellung der logarithmierten Gleichung \ref{zielfkt3} ist in Abb. \ref{fig:ces_3_3_1} ersichtlich. Darin sind die verschiedenen Materialien eingetragen.\\
\begin{figure}[H]
	\centering
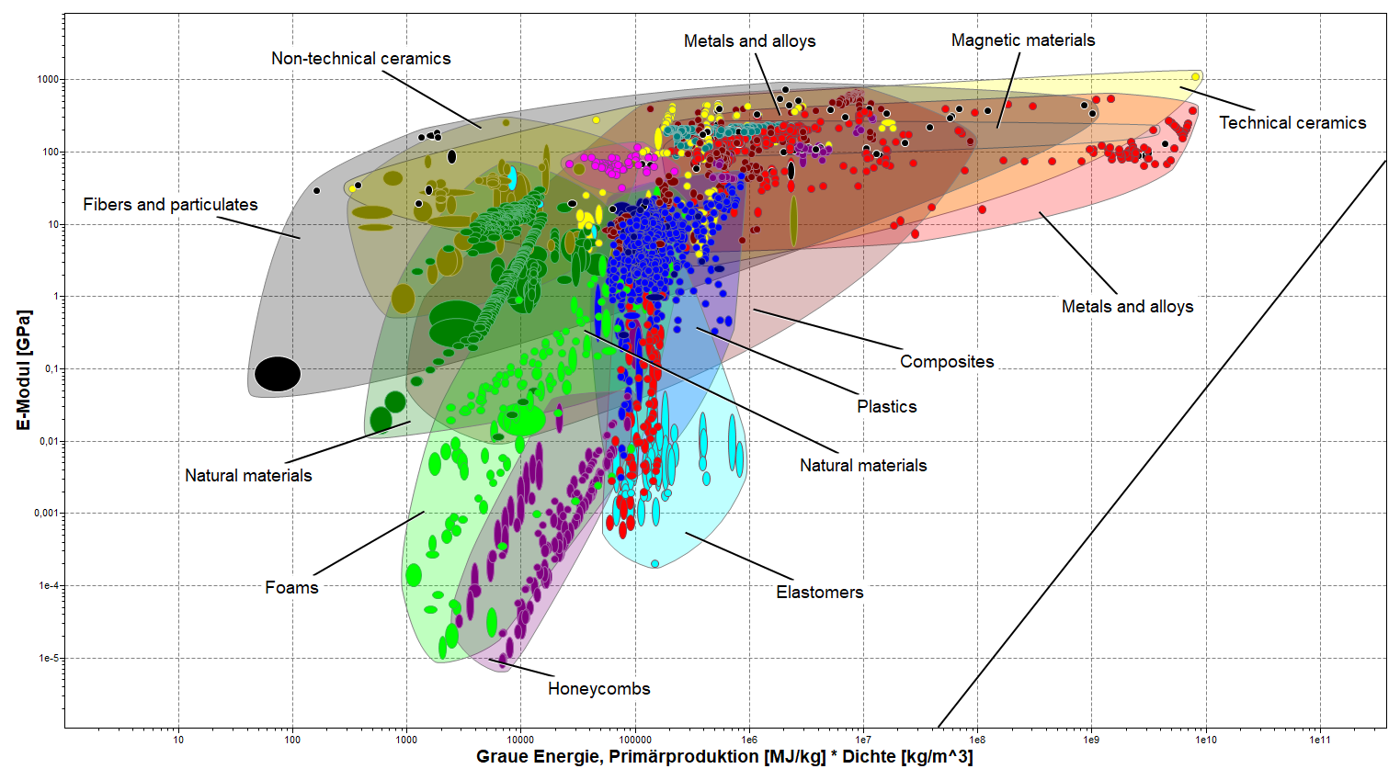
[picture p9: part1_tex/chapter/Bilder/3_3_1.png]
	
	\caption{Eigenschaftsdiagramm für die Werkstoffauswahl die Tablettenrutsche inklusive der Designgeraden mit der Steigung 2}
	\label{fig:ces_3_3_1}
\end{figure}
Hinzufügen aller Randbedingungen schließt einige Materialien aus, Abb. \ref{fig:ces_3_3_2}\\
\begin{figure}[H]
	\centering
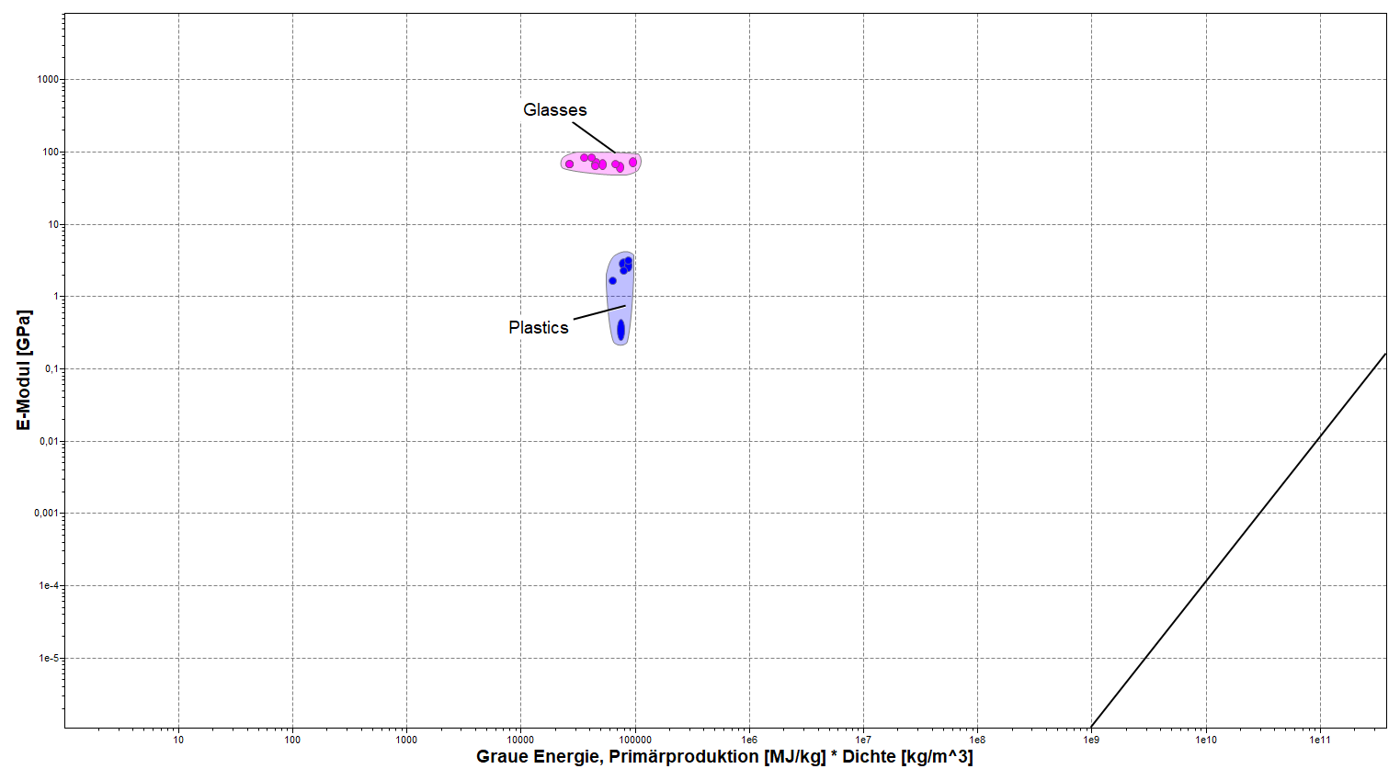
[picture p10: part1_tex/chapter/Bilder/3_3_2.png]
	
	\caption{Eigenschaftsdiagramm aller möglicher Materialien für die Tablettenlagerung unter Berücksichtigung der Randbedingungen mit leicht verschobener Designgerade}
	\label{fig:ces_3_3_2}
\end{figure}
Durch Verschieben der Gerade bleiben die fünf Materialien mit dem höchsten Materialindex übrig (Abb. \ref{fig:ces_3_3_3}).\\
\begin{figure}[H]
	\centering
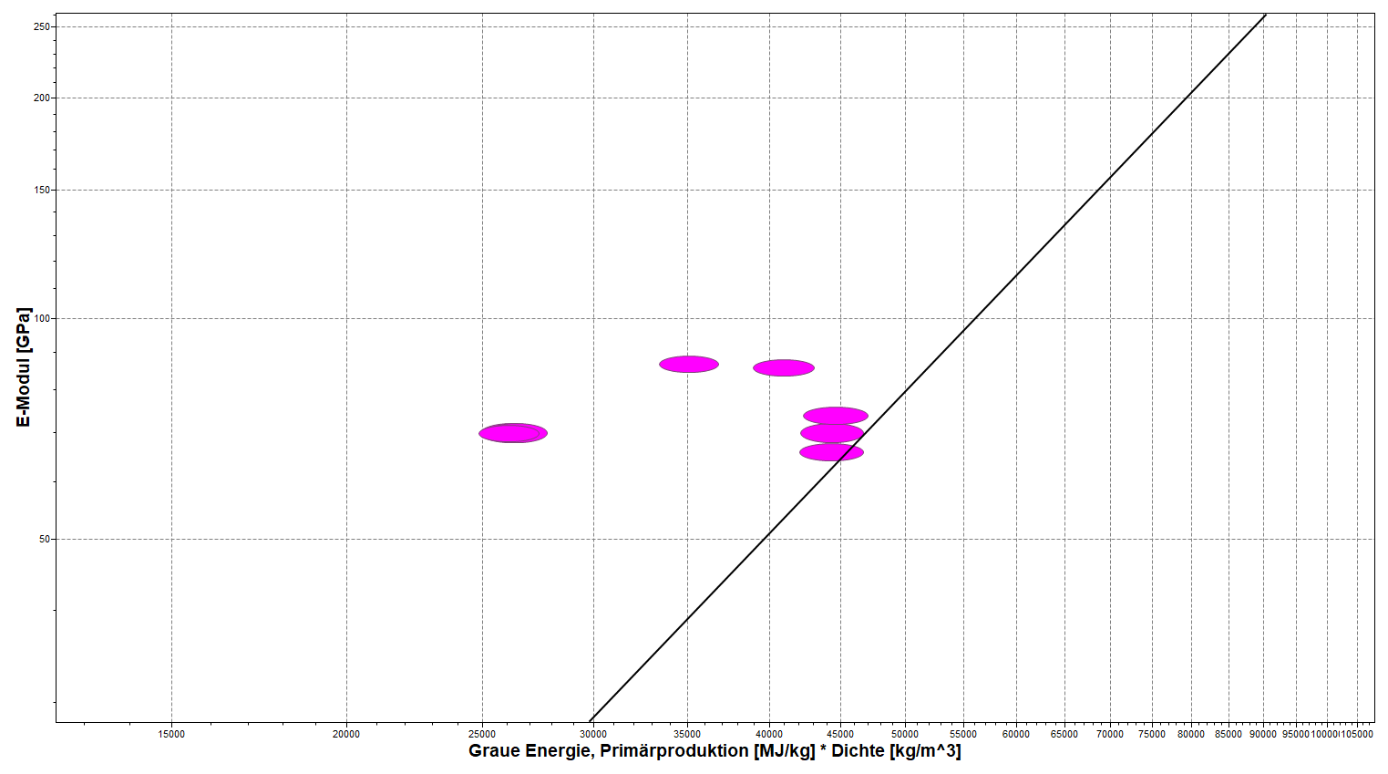
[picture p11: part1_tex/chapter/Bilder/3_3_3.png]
	
	\caption{Top 5 Materialien für die Tablettenlagerung nach der Ashby-Methode}
	\label{fig:ces_3_3_3}
\end{figure}
Zu den geeignetsten Materialien gehören:
\begin{itemize}
	\item[1)] Kalk-Natron-Glas (Materialindex: 3,21$\,\times10^{-4}$)
	\item[2)] Aluminiumsilicate (3,2$\,\times10^{-4}$) 
	\item[3)] Kali-Natron-Zink-Glas (1,93$\,\times10^{-4}$)
	\item[4)] Low E-Glas (1,89$\,\times10^{-4}$)
	\item[5)] Natron-Zinkglas (1,84$\,\times10^{-4}$)
\end{itemize}
Kalk-Natron-Glas findet häufig Anwendung zur Fertigung von Behälterglas, wodurch es sich sehr gut als Material für die Lagerungsbehälter eignet. Es wird bei circa 1.200°C eingeschmolzen und kristallisiert als Silicatglas in allen möglichen Formen. 

\section{Aktoren}
Die \textbf{Funktion} der Aktoren ist es die rotatorische Bewegung der Servomotoren in eine translatorische Bewegung umzusetzen und dadurch den Vortrieb eines Schiebers zu erzeugen, wodurch die Tabletten aus der Lagerung geschoben werden. Der prinzipielle Aufbau ist in Abb. \ref{fig:3_6_a} gezeigt. 
\begin{figure}[H]
	\centering
	
	\caption{Baugruppe der Aktoren}
	\label{fig:3_6_a}
\end{figure}
Das methodische Selektieren des Werkstoffes für die Baugruppe wird im Folgenden stellvertretend für alle Bauteile am kritischsten Teil, dem Pleuel 2, durchgeführt. Es wirkt auf alle umliegenden Komponenten, die zu dieser Baugruppe gehören, der selbe Belastungszustand, wobei dieser Pleuel im Querschnitt am dünnsten ist, und daher zuerst versagt. Durch die Anordnung und Funktionsweise wird der Pleuel auf Zug/Druck belastet, Abb. \ref{fig:3_6_b}.
\begin{figure}[H]
	\centering
	
	\caption{Axial belasteter Balken als abstrahierte Pleuelstange}
	\label{fig:3_6_b}
\end{figure}
Die \textbf{Randbedingungen} hierfür lauten:
\begin{itemize}
	\item Material muss recyclebar sein
	\item Material muss ein guter Isolator sein, bzw. $\rho_e\,>\,10^{19}\,\mu\Omega$cm
	\item Preis $\le\,1,5\,\frac{\text{€}}{\text{kg}}$
\end{itemize}
Das \textbf{Ziel} für die Materialauswahl liegt in der Minimierung der Kosten, um eine hohe Wirtschaftlichkeit des Produktes zu erreichen. Als \textbf{freie Variable} tritt neben der Wahl des Materials die Querschnittfläche des Pleuels auf.\\
Die Gesamtkosten berechnen sich durch:
\begin{equation}
	K\,=\,C_m\,m\,=\,C_m\,\rho\,V\,=\,C_m\,\rho\,A\,l\,.
\end{equation}
Sie können durch Reduzierung der Masse und damit letztendlich durch Reduzierung der Querschnittfläche minimiert werden. Es gilt jedoch, dass mindestens die Zugkraft $F$ ausgehalten werden muss, ohne dass eine plastische Verformung eintritt. Daher folgt
\begin{equation}
	\frac{F}{A}\,\le\,\sigma_y\,,
\end{equation}
wobei $sigma_y$ der Streckgrenze entspricht.
Durch Eliminierung der Querschnittfläche folgt
\begin{equation}
K\,\ge\,C_m\,l\,\,F\,\frac{\rho}{\sigma_y}\,.
\end{equation}
Umstellen liefert die Performance-Gleichung unter Vernachlässigung fester Parameter
\begin{equation}\label{performance34}
P_{CR}^{3.4}\,=\,\frac{1}{K}\,=\,\frac{\sigma_y}{\rho}\,,
\end{equation}
wobei $P_{CR}^{3.4}$ der unter den vorgegebenen Randbedingungen der zu maximierende Materialindex ist. Die graphische Darstellung der Ashby-Methode von Gleichung \ref{performance34} über logarithmierten Achsen sowie der Indexgeraden mit der Steigung 1 ist in Abb. \ref{fig:ces_3_4_1} dargestellt.\\
\begin{figure}[H]
	\centering
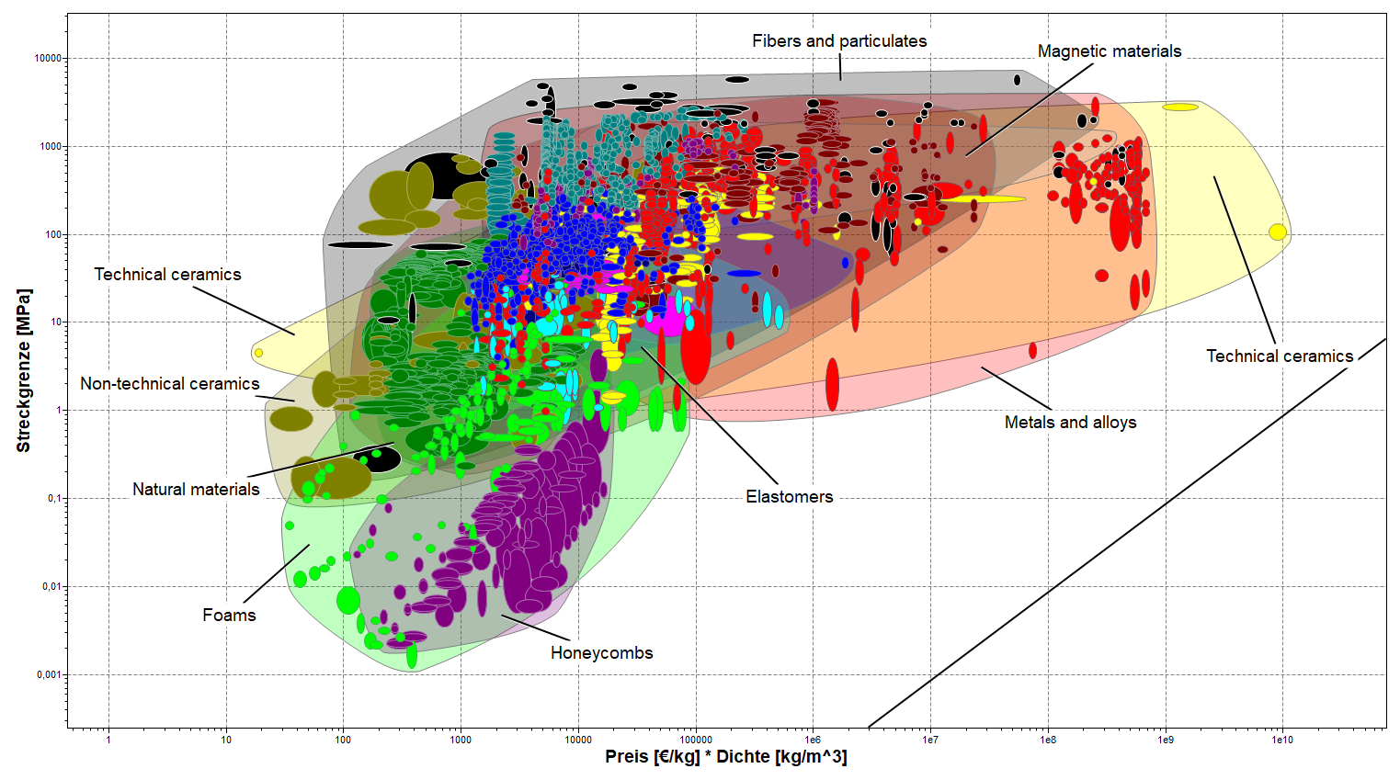
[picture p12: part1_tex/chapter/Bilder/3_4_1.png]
	
	\caption{Eigenschaftsdiagramm für die Werkstoffauswahl die Aktoren0 inklusive der Designgeraden mit der Steigung 1}
	\label{fig:ces_3_4_1}
\end{figure}
Alle nach Hinzufügen der Randbedingungen übrigen Materialien sind in Abb. \ref{fig:ces_3_4_2} dargestellt.\\
\begin{figure}[H]
	\centering
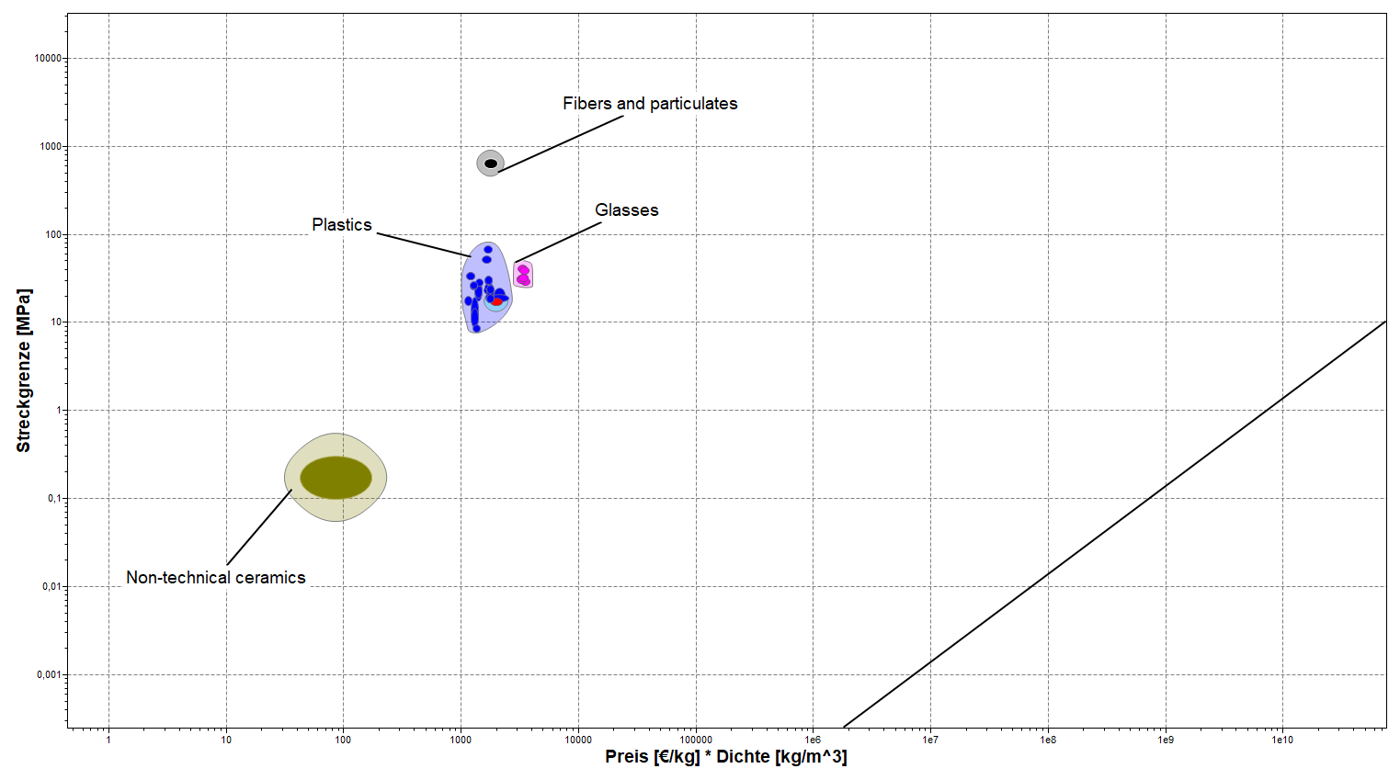
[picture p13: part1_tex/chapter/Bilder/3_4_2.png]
	
	\caption{Eigenschaftsdiagramm aller möglicher Materialien für die Aktoren unter Berücksichtigung der Randbedingungen mit leicht verschobener Designgerade}
	\label{fig:ces_3_4_2}
\end{figure}
Verschieben der Designgeraden liefert die für den Anwendungsfall am besten geeigneten Materialien (Abb. \ref{fig:ces_3_4_3}).\\
\begin{figure}[H]
	\centering
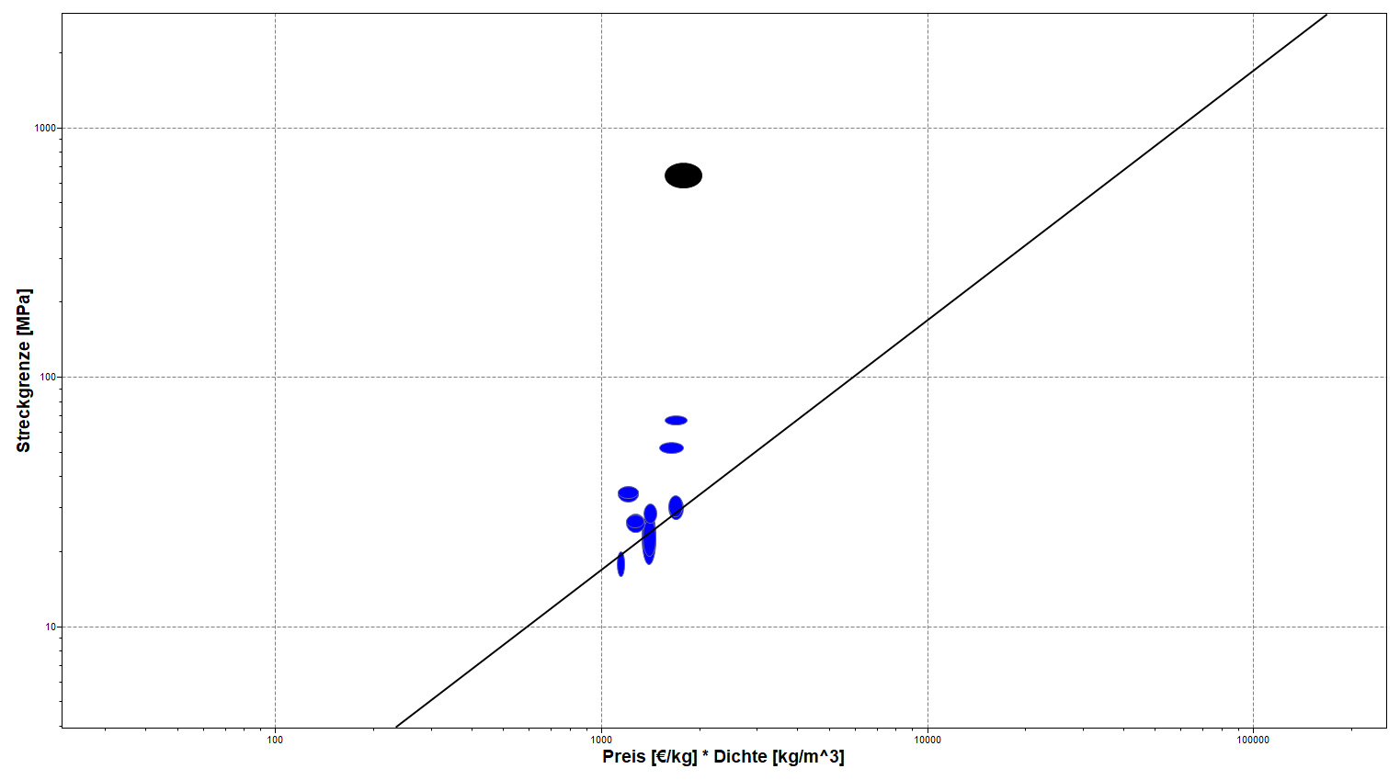
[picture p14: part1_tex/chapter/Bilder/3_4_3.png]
	
	\caption{Top 5 Materialien für die Aktoren nach der Ashby-Methode}
	\label{fig:ces_3_4_3}
\end{figure}
Die daraus resultierenden Materialien sind:
\begin{itemize}
	\item[1)] Polyesterfasern (Materialindex: 0,364)
	\item[2)] Polyethylenterephthalat (PET, 0,04) 
	\item[3)] Polypropylen (PP, 0,0287)
	\item[4)] Polyethylen (PE - HD, high density, 0,0203)
	\item[5)] Polyethylen (PE - MD, mid density, 0,0157)
\end{itemize}
Polyesterfasern sind jedoch lediglich für den Einsatz in Verbundwerkstoffen geeignet und können nicht als ganzheitliches Material dienen. Polyethylenterephthalat hingegen weist immernoch gute mechanische Eigenschaften auf und kann gegebenenfalls auch mit Polyesterfasern verstärkt werden, um höheren Belastungen standzuhalten. Daher fällt die Wahl des Materials auf PET.

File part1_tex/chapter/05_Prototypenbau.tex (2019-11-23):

% !TeX encoding = UTF-8
% !TeX root = ../Vitamintablettenspender.tex

\chapter{Prototypenbau}

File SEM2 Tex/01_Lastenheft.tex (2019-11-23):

\chapter{Lastenheft}

Es ist die Entwicklung eines innovativen Haushalt-Gadgets in AM-\&Multimaterial-Design vorgegeben. Dabei soll ein bedeutsames aber zeitgleich auch revolutionäres und innovatives Produkt entworfen werden. Vom Kunde ist ein Vitamintablettenspender gewünscht. Dieser soll über folgende Funktionen verfügen:
\begin{itemize}
\item Aufbewahrungsmöglichkeit für vier unterschiedliche Vitamintablettensorten
\item Automatischer Tablettenauswurf in einen Trinkbehälter
\item Automatisches Auffüllen des Trinkbehälters mit Wasser
\item Handlich
\item Leicht
\end{itemize}
Dazu wurden zusätzliche Kundenbefragungen und Umfragen hinsichtlich wünschenswerter Zusatzfunktionen durchgeführt. Als begeisternde Kriterien wurden folgende Wunschanforderungen formuliert:
\begin{itemize}
\item Touchdisplay zur Bedienung
\item Füllstandanzeige der Tablettenreservoirs
\item großer Wasserbehälter
\end{itemize}
Das Produkt soll dem Kunden im Februar 2020 mittels einem fertigen Prototypen vorgestellt werden.

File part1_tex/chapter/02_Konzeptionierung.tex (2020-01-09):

% !TeX encoding = UTF-8
% !TeX root = ../Vitamintablettenspender.tex

\chapter{Konzeptionierung}

Im Entwicklungsprozess nimmt die Suche nach der optimalen Lösung für das vom Kunden gewünschte Produkt die Hauptaufgabe ein. Das Ergebnis soll nachvollziehbar und objektiv bewertbar sein. Dafür wird im Folgenden zunächst eine umfassende Planung des Produktes hinsichtlich Markt- und Wettbewerbschancen durchgeführt.

Die Entwicklung des Konzepts erfolgt darauffolgend anhand eines Projektplans, der den vom Kunden gewünschten Termin zur Vorstellung des Produktes mit einem Prototypen berücksichtigt. In der Anforderungsliste werden die Anforderungen des Kunden aus dem Lastenheft konkretisiert und durch interne Spezifikationen ergänzt. Damit wird eine Basis zur Entwicklung von Lösungsideen geschaffen.

Hierfür werden zunächst die Zusammenhänge von Anforderungen und Funktionen abstrakt in der Funktionsstruktur dargestellt, wobei das Loslösen vom Gegenständlichen und von vorzeitigen Festlegungen auf ein bestimmtes Lösungskonzept ermöglicht wird. Zur Systematisierung der Suche und Auswahl des optimalen Lösungsprinzips wird im morphologischen Kasten alle Lösungsoptionen aller Teilfunktionen berücksichtigt und verschiedene Gesamtlösungskombinationen unter Beachtung von Konflikten untereinander gebildet. Die abgesicherte Festlegung des zu realisierenden Lösungskonzeptes erfolgt in der Nutzwertanalyse. Zuletzt wird ein Grobentwurf zur Verdeutlichung des Wirkprinzips angefertigt.

\section{Produktplanung}
Der Markt für Nahrungsergänzungsmittel ist riesig. Mehrere Studien und Umfragen zeigten bereits die enorme Nachfrage deutschlandweit. So wurden nach einer Studie von Insight Health \cite{LMV}, die auf der Website des deutschen Lebensmittelverbandes veröffentlicht wurde, dass im Jahr 2018 225 Millionen Packungen Nahrungsergänzungsmittel verkauft wurden. Das entspricht einem Umsatz von circa 1,439 Milliarden Euro. Dabei machen Vitamine und Mineralstoffe näherungsweise zwei Drittel des gesamten Nahrungsergänzungsmittel-Marktes aus. Das Vitamin C, zur Stärkung des Immunsystems, ist dabei in der Sparte der Vitaminprodukte mit großem Abstand am beliebtesten, sodass davon im Jahr 2019 29,2 Millionen Packungen abgesetzt wurden. Zweitplatziert sind Multivitamin-Tabletten mit Mineralstoffen, die immer noch 17,5 Millionen verkaufte Packungen vorweisen können. Aber auch Vitamintabletten, die lediglich das Vitamin B12 oder die Vitamine A/D oder B-Komplexe beinhalten, sind sehr stark gefragt.

Unabhängig von Vitaminen werden einige Mineralstoffe wie Magnesium insbesondere für Sportler oder Calcium vom Markt aufgekauft. Dabei wurden im Jahr 2018 36,8 Millionen Packungen Magnesium sowie 16,4 Millionen Packungen Calcium verkauft. Die Chancen, dass ein Produkt zur automatisierten Ausgabe von Tabletten mit Vitaminen und Mineralen vertrieben wird, sind damit gegeben. Die bereits große Akzeptanz von Medikamentendispensern stellen ein gutes Beispiel für die Erfolgsaussichten des zu entwickelnden Produktes. Diese Dispenser verringern die Wahrscheinlichkeit falsche Medikamente einzunehmen und bieten dabei zeitgleich einen hohen Komfort. Mit dem Vitamintablettenspender wird ein Produkt konstruiert, das der breiten Masse der Bevölkerung zugänglich gemacht werden kann. Aufgrund der hohen Verkaufszahlen von Nahrungsergänzungsmitteln bieten sich Chancen durch den erhöhten Komfort der Tablettenzubereitung und der damit erleichterten Einnahme. Außerdem kann die Aufbewahrung verschiedener Vitamin- und Mineralsorten die Vielfältigkeit in der Nachfrage nach Nahrungsergänzungsmitteln kompensieren.

Die Technologien zum Realisieren des Produktwunsches sind gegeben. Es gibt zahlreiche Möglichkeiten zum Entwerfen eines Ausgabemechanismus von Vitamintabletten. Da technologisch größtenteils nur Motoren zum Erzeugen des gewünschten Schiebeprinzips eingesetzt werden müssen, treten bei der Umsetzung ausschließlich Komponenten der Technologien aus dem Bereich der Basis- oder der Alten Technologien auf. Diese sind preislich günstig zu bekommen und können durch geschickte Kombination miteinander Gewinne einbringen. Beispielsweise wurden in Norwegen im Jahr 2018 elektronische Medikamentendispenser in Krankenhäuser in einem Pilotprojekt getestet \cite{schneider}, wodurch bestätigt wird, dass die technischen Voraussetzungen für das Produkt gegeben sind.

Im direkten Wettbewerb mit dem automatischen Vitamintablettenspender steht ein Produkt der Firma Tespo (Plymouth, England) \cite{tespo}, das die automatische Ausgabe ihrer eigenen Vitaminprodukten in Pulverform ermöglicht. Dieses Produkt ist jedoch nicht für den Massenmarkt und herkömmliche Vitamintabletten geeignet. Des Weiteren gibt es Behältnisse zu Aufbewahrung von Tabletten. Diese stellen jedoch nicht die automatische Ausgabe sowie das anschließende Auffüllen des Trinkbehältnisses mit Wasser bereit. Die gewünschte Bedienbarkeit mit einem Touchdisplay sind zusammen mit der automatischen Zubereitung Alleinstellungsmerkmale. Damit ist das Produkt ein Unikat und hebt sich gegenüber der Konkurrenz deutlich ab.

In der Patentanalyse wurde mittels der Bottom-Up-Recherche-Methode sichergestellt, dass es keine vergleichbaren Patente des Produkts gibt. Dabei wurden im Depatisnet, Espacenet sowie unter Google Patents keine relevanten Produkte gefunden. Es existiert ausschließlich das deutsche Patent DE000029811862U1 \cite{patent} mit dem Titel "Vitamin-Tablettenspender". Das im Jahr 1998 angemeldete Gebrauchsmuster beschreibt einen Spender, an dem Tablettenröhrchen befestigt werden können. Mit Hilfe eines mechanischen Schiebers können einzelne Tabletten herausgenommen werden. Für die Konstruktion ist die Montage an der Wand vorgesehen, wobei dort die einzelnen Tablettenröhrchen ausgetauscht werden können. Das Patent beinhaltet das Funktionsprinzip des zu entwickelnden Produktes nur eingeschränkt. Geschützt wird eine komplette Wandhalterung, bei der die Befestigung mittels Verschrauben der Produktschenkel erfolgt.

Des Weiteren wird die direkte Montage der Röhrchen sowie der mechanischen Schieber zum Herausnehmen der Tabletten patentiert. Das zu entwickelnde Produkt erweitert das Prinzip in seiner Funktion, sodass der Wirkbereich des Schutzes verlassen wird. Der automatische Prozess zur Tablettenausgabe löst dabei den Schiebemechanismus ab, sollte jedoch hinsichtlich seiner Ähnlichkeit zum mechanischen Schieber überprüft und abgesichert werden. Das System ist nicht zur Montage an der Wand vorgesehen. Außerdem ist die Befüllung des Gerätes mit den Tabletten angedacht, sodass die einzelnen Röhrchen nicht direkt am Produkt montiert werden. Durch Hinzufügen von wesentlichen Produktfunktionen wie beispielsweise einem Touchscreen, einem Wasserbehälter zum automatischen Auffüllen des Trinkbehälters und einigen weiteren Zusatzfunktionen hebt sich das System deutlich vom Patent ab und kann konstruiert werden. Die Kombination der einzelnen Komponenten für sein Anwendungsgebiet kann als Patent angemeldet werden.

\section{Projektplan}
\begin{figure}[H]
	\centering
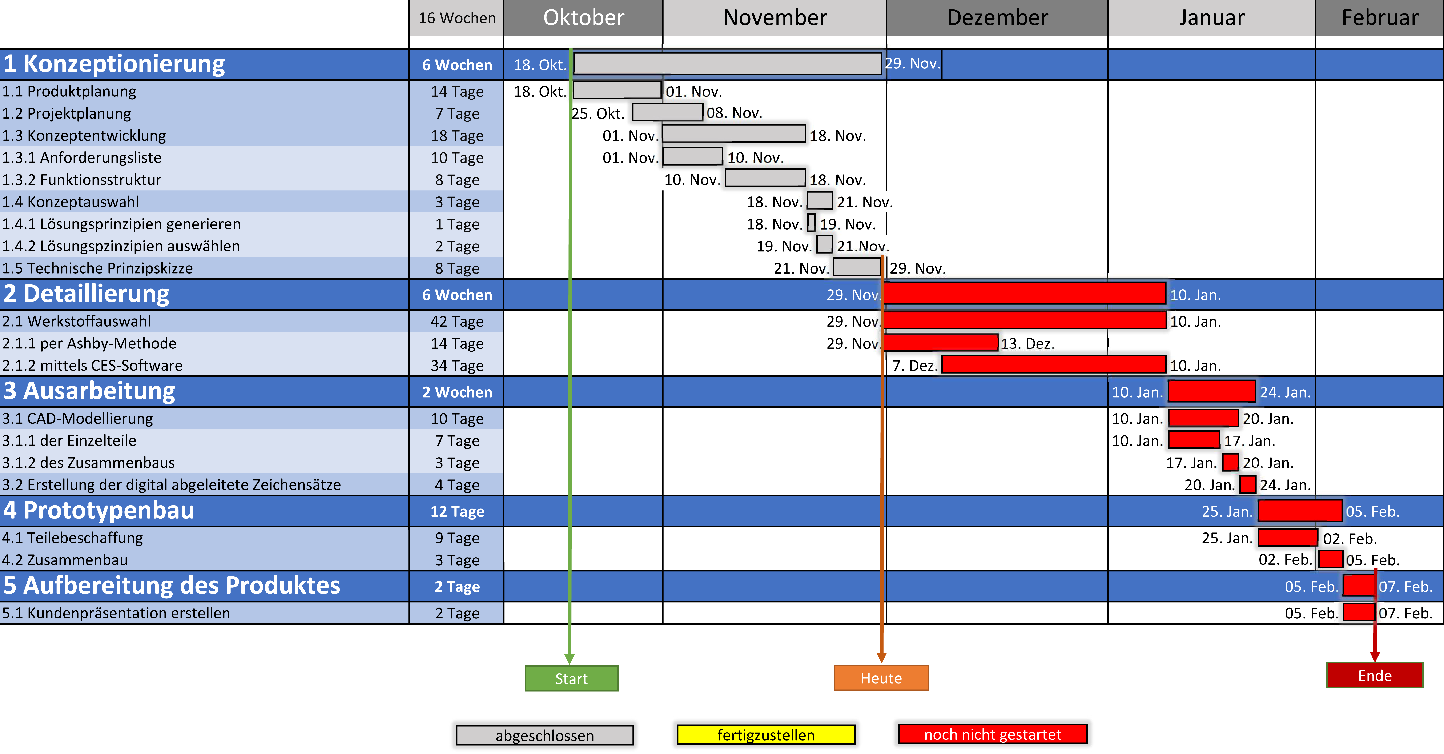
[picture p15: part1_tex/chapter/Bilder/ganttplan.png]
	 
	\caption{Projektplan}
\end{figure}

\section{Anforderungsdefinition}

\newcolumntype{L}[1]{>{\raggedright\arraybackslash}p{#1}} % linksbündig mit Breitenangabe
\newcolumntype{C}[1]{>{\centering\arraybackslash}p{#1}} % zentriert mit Breitenangabe
\newcolumntype{R}[1]{>{\raggedleft\arraybackslash}p{#1}} % rechtsbündig mit Breitenangabe

\begin{longtable}{C{0.03\linewidth}C{0.05\linewidth}C{0.05\linewidth}L{0.5\linewidth}C{0.14\linewidth}C{0.07\linewidth}}
	\toprule	
 	\textbf{Nr.} & \textbf{F/W} & \textbf{Gew.} & \textbf{Beschreibung und Erläuterung} & \textbf{Faktortyp} & \textbf{Ver.}\\	
	\toprule
	\endfirsthead
	\toprule
	\textbf{Nr.} & \textbf{F/W} & \textbf{Gew.} & \textbf{Beschreibung und Erläuterung} & \textbf{Faktortyp} & \textbf{Ver.}\\
	\toprule
	\endhead
	\textbf{1} & & & \textbf{Funktionsanforderungen} && \\
	1.1 & F & & Automatische Ausgabe einer Vitamintablette nach Wahleingabe über einen Auswurf in einen Trinkbehälter & Basis & KK/TG\\
	1.2 & W & 9 & Ausgabe sollte innerhalb 15 Sekunden nach Wahleingabe erfolgen & Leistung & KK/TG\\
	1.3 & W & 6 & Automatische Ausgabe einer Tablette bei Platzierung eines Trinkbehälters unter den Auswurf&Begeisterung& KK/TG\\
	1.4 & W & 10 & Automatisches Auffüllen des Trinkbehälters mit Wasser nach Tablettenausgabe &Begeisterung& KK/TG\\
	1.5 & W & 4 & Es sollte nur eine der Tageszeit entsprechende Tablette ausgegeben werden, um die Vitaminbalance des Nutzers zu garantieren &Begeisterung& KK/TG \\
	1.6 & F & & Aufbewahrungs- und Ausgabemöglichkeit für mindestens zwei unterschiedliche Vitamintablettensorten & Basis & KK/TG\\
	1.7 & F & & Aufbewahrungsmöglichkeit für mindestens 20 Brausetabletten je Vitamintablettensorte & Basis & KK/TG\\
	1.8 & F & & Anzeige der aktuellen Uhrzeit & Basis & KK/TG\\
	1.9 & W & 5 & Anzeige des nächsten Tablettentyps, der vom Nutzer eingenommen werden soll, um eine regelmäßigen Tabletteneinnahme zu überwachen &Begeisterung& KK/TG\\
	1.10 & W & 4 & Anzeige der Uhrzeit für die vom Nutzer als nächstes zu nehmende Tablette &Begeisterung& KK/TG\\
	1.11 & W & 3 & Warnton, wenn Uhrzeit von Anforderung 1.10 für einen Nutzer um fünf Minuten überschritten wurde &Begeisterung& KK/TG\\
	1.12 & W & 2 & Verschiedene Nutzerprofile, sodass die Überwachung der regelmäßigen Tabletteneinnahme für mehrere Nutzern erfolgen kann &Begeisterung& KK/TG\\
	1.13 & W & 10 & Bedienung per Touchdisplay &Begeisterung& KK/TG\\
	1.14 & W & 10 & Füllstandsanzeige der Tablettenreservoirs &Begeisterung& KK/TG\\
	
	\midrule
	\newpage
	\textbf{2} & & & \textbf{Mechanische/Geometrische Anforderungen} &&\\
	2.1 & F & & Kompatibel für handelsübliche Vitamintabletten mit den Abmaßen: $\text{Durchmesser}\,\times\,\text{Höhe}\,=\,25\,\text{mm}\,\times\,6\,\text{mm}$ & Leistung  & KK/TG\\
	2.2 & F & & Maximales Gewicht: $5\,\text{kg}$ & Leistung & KK/TG\\
	2.3 & F & & Maximale Abmessungen: $\text{Länge}\,\times\,\text{Breite}\,\times\,\text{Höhe}\,=\,300\,\text{mm}\,\times\,300\,\text{mm}\,\times\,450\,\text{mm}$ & Leistung  & KK/TG\\
	2.4 & F & & Geeignet für alle Trinkbehälter mit den maximalen Abmessungen: $\text{Durchmesser}\,\times\,\text{Höhe}\,=\,90\,\text{mm}\,\times\,180\,\text{mm}$ & Leistung & KK/TG\\
	
	\midrule
	
	\textbf{3} & & & \textbf{Sicherheitsanforderungen} &&\\
	3.1 & F & & Schutz des mechanischen Tablettenauswurfs & Basis & KK/TG\\
	3.2 & F & & Keine scharfen Kanten & Basis & KK/TG\\
	3.3 & F & & Im Betrieb kein Zugang zu elektrischen Bauteilen möglich & Basis & KK/TG\\
	
	\midrule 
	
	\textbf{4} & & & \textbf{Umwelt- und Wartungsanforderungen} &&\\
	4.1 & W & 3 & Gehäuses soll recyclebar sein & Leistung & KK/TG\\
	4.2 & F & & Wartungsintervall: 1x jährlich & Leistung & KK/TG\\
	
	\midrule
	
	\textbf{5} & & & \textbf{Produktions- und Fertigungsanforderungen}&& \\
	5.1 & F & & Funktionsprototyp bis zum 07.02.2020 & Leistung & KK/TG\\
	5.2 & F & & Gehäuse des Prototyps mittels RPT per 3D-Druck & / & KK/TG\\
	5.3 & F & & Verwendung wasserfester Materialien &Basis& KK/TG\\
	5.4 & F & & Norm- und Zukaufteile zu bevorzugen & / & KK/TG\\
	5.5 & F & & Motoren des automatischen Auswurfs als Zukaufteile & / & KK/TG\\
	5.6 & W & 8 & Pumpe zum Auffüllen des Trinkbehälters sollte für Anforderung 1.4 ein Zukaufteil sein & / & KK/TG\\
	5.7 & W & 6 & Verwendung robuster Sensoren mit einer Lebensdauer $>\, 50.000\,$h & Leistung & KK/TG\\
	
	\midrule
	
	\textbf{6} & & & \textbf{Sonstige Anforderungen} &&\\
	6.1 & F & & Betrieb über eine haushaltsübliche 230V Steckdose & Basis &\\
	
	\bottomrule
	
	\caption{Anforderungsliste (F$\,=\,$Festanforderung, W$\,=\,$Wunschanforderung, Gew.$\,=\,$Gewichtung, Ver.$\,=\,$Verantwortlicher)}
	\label{anforderungsliste}
\end{longtable}

\begin{figure}[H]
	\centering
	
	\caption{Konsistenzmatrix}
	\label{fig:konsistenzmatrix}
\end{figure}

\FloatBarrier
\begin{figure}[h!]
	\centering
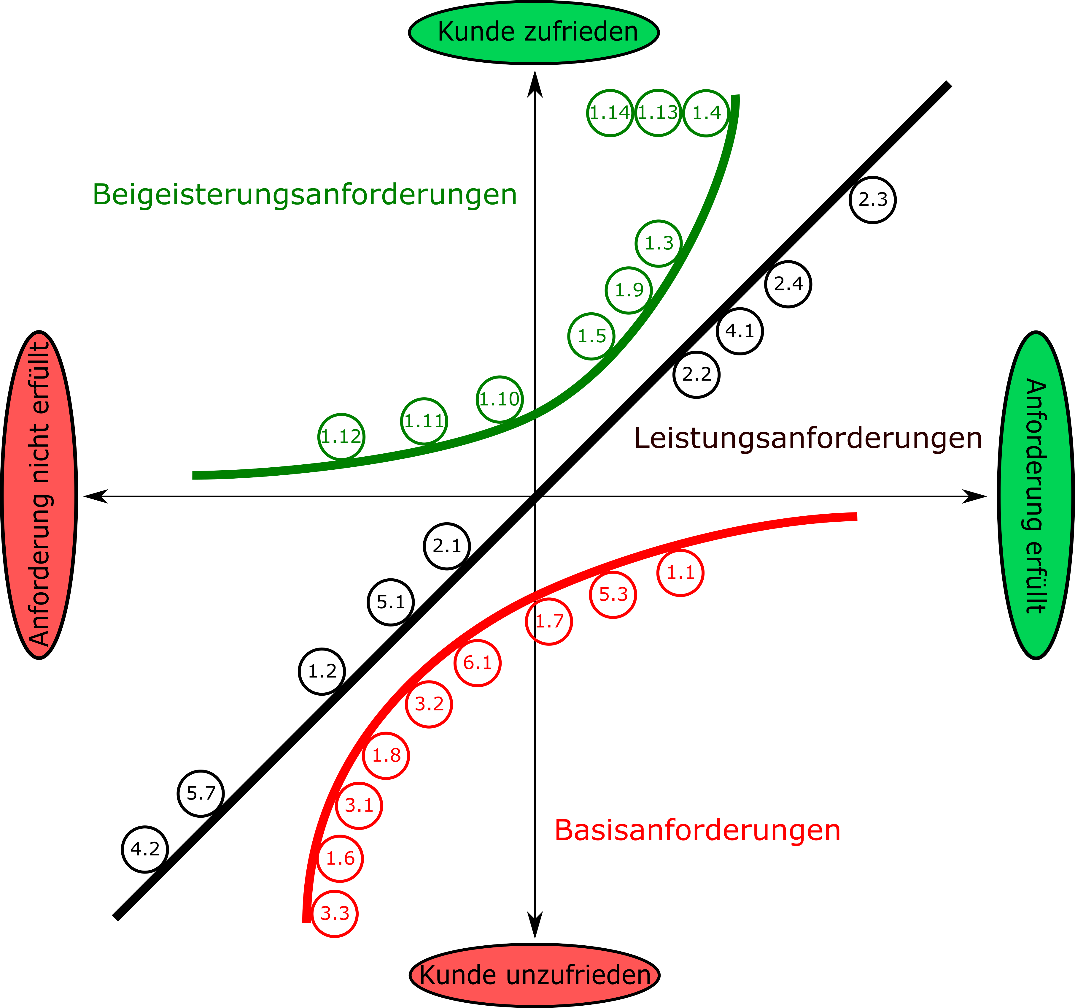
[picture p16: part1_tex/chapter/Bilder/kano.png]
	 
	\caption{Verdeutlichung der Lage der Anforderungen im Kano-Diagramm}
\end{figure}

\newpage
\section{Funktionsstruktur}

\begin{figure}[H]
	\centering
	
	\caption{Allgemeine kybernetische Black-Box-Darstellung}
	\label{fig:funktionsstrukturkybernetisch}
\end{figure}

\begin{figure}[H]
	\centering
	
	\caption{Hierarchische Funktionsstruktur}
	\label{fig:funktionsstrukturhierarchisch}
\end{figure}

\begin{figure}[H]
	\centering
	
	\caption{Funktionsmodell mit Darstellung der  wichtigsten Funktionen}
	\label{fig:funktionsmodell}
\end{figure}

\newpage
\section{Lösungsprinzipien}

\begin{figure}[H]
	\centering
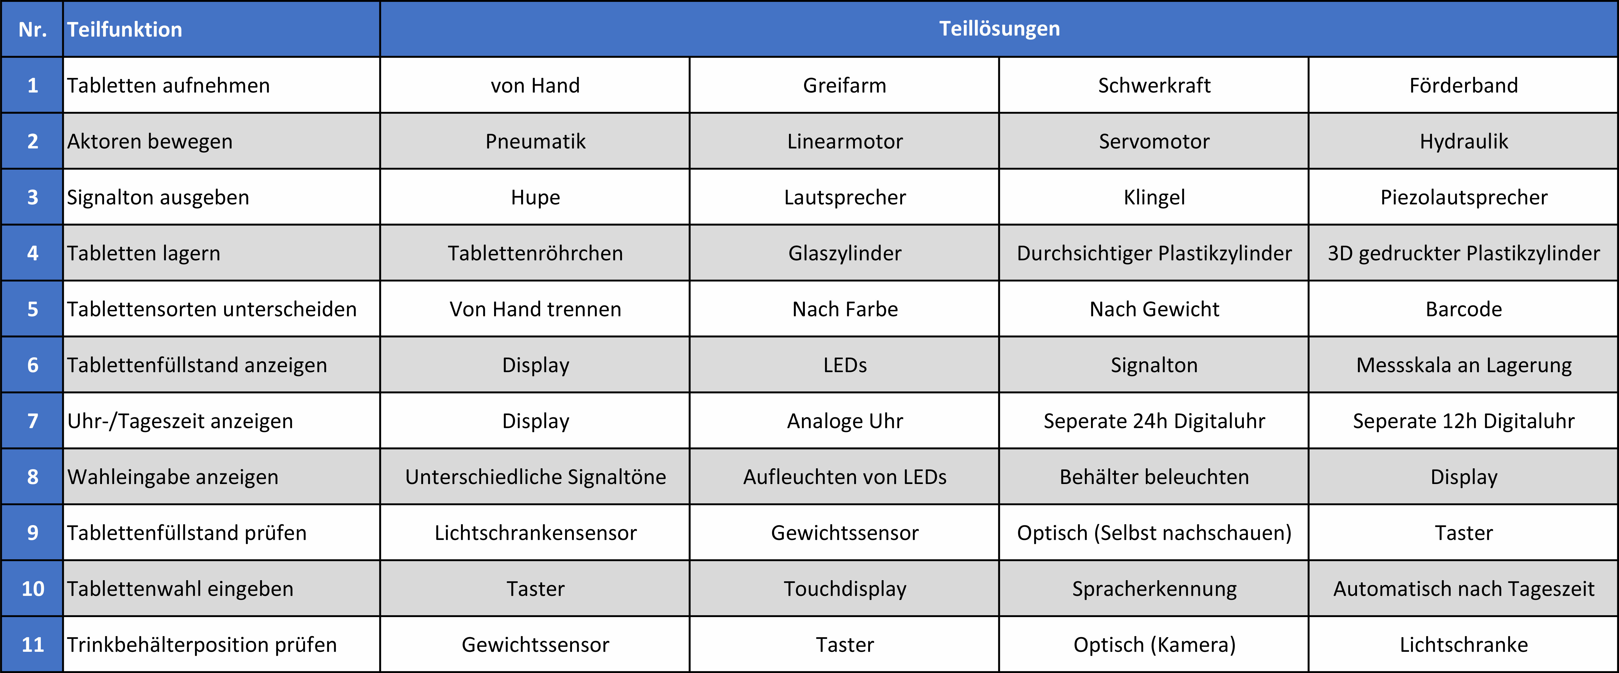
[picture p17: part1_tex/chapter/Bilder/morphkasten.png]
	
	\caption{Morphologischer Kasten}
	\label{fig:morphkasten}
\end{figure}

\begin{figure}[H]
	\centering
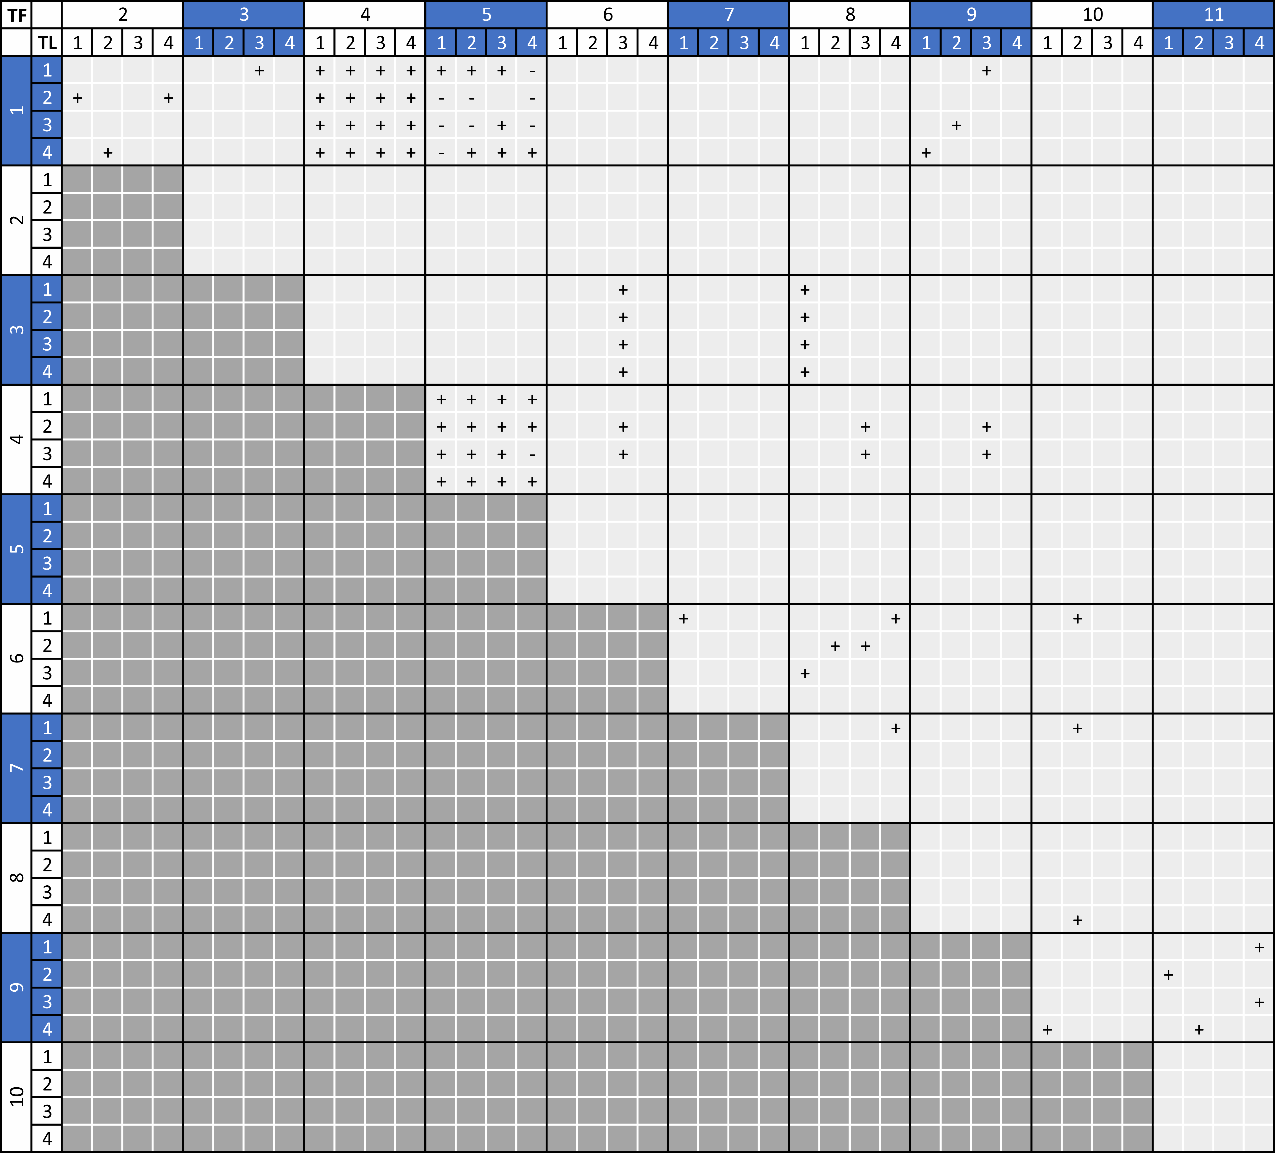
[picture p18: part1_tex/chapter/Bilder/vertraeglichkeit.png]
	
	\caption{Verträglichkeitsmatrix}
	\label{fig:vertraglichkeit}
\end{figure}

\begin{figure}[H]
	\centering
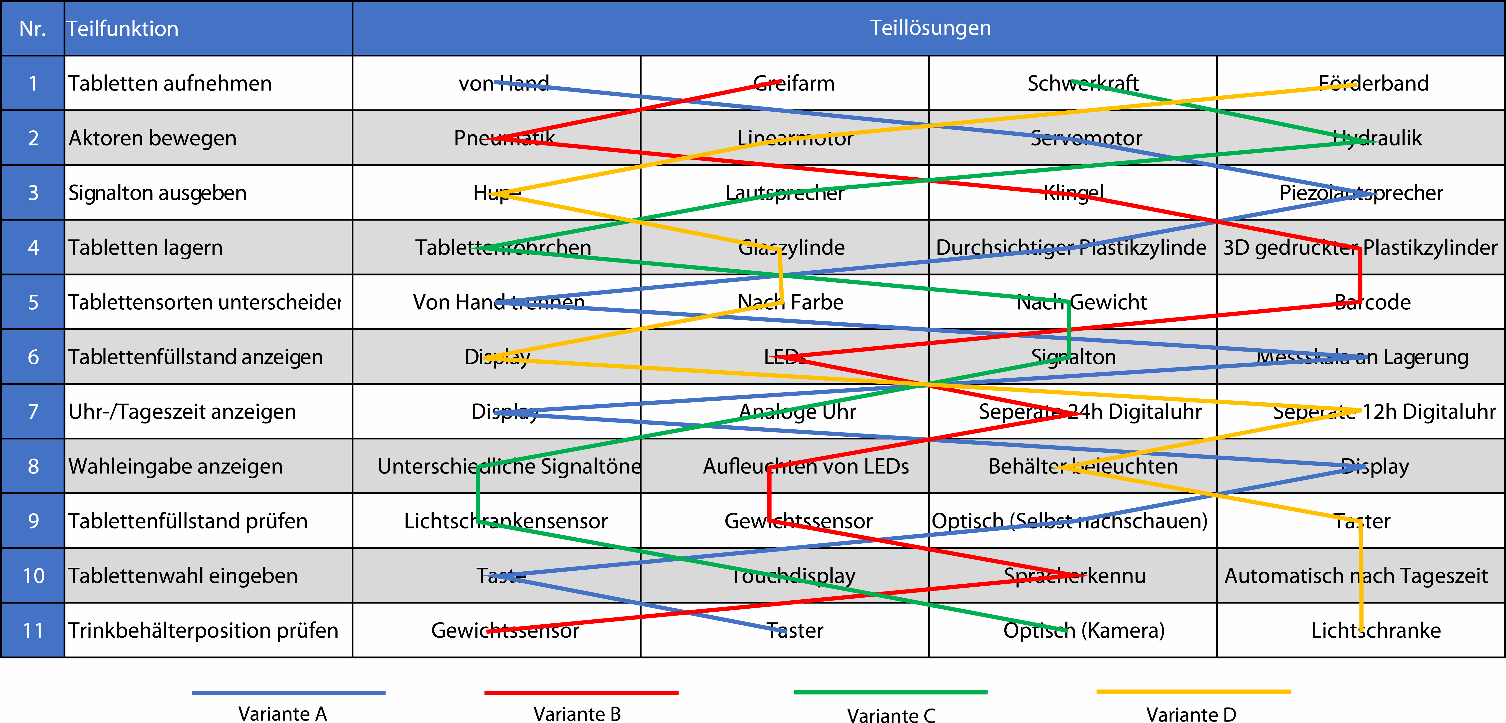
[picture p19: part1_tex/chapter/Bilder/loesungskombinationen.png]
	
	\caption{Kennzeichnungen von vier möglichen Gesamtlösungskombinationen}
	\label{fig:losungskombinationen}
\end{figure}

\begin{figure}[H]
	\centering
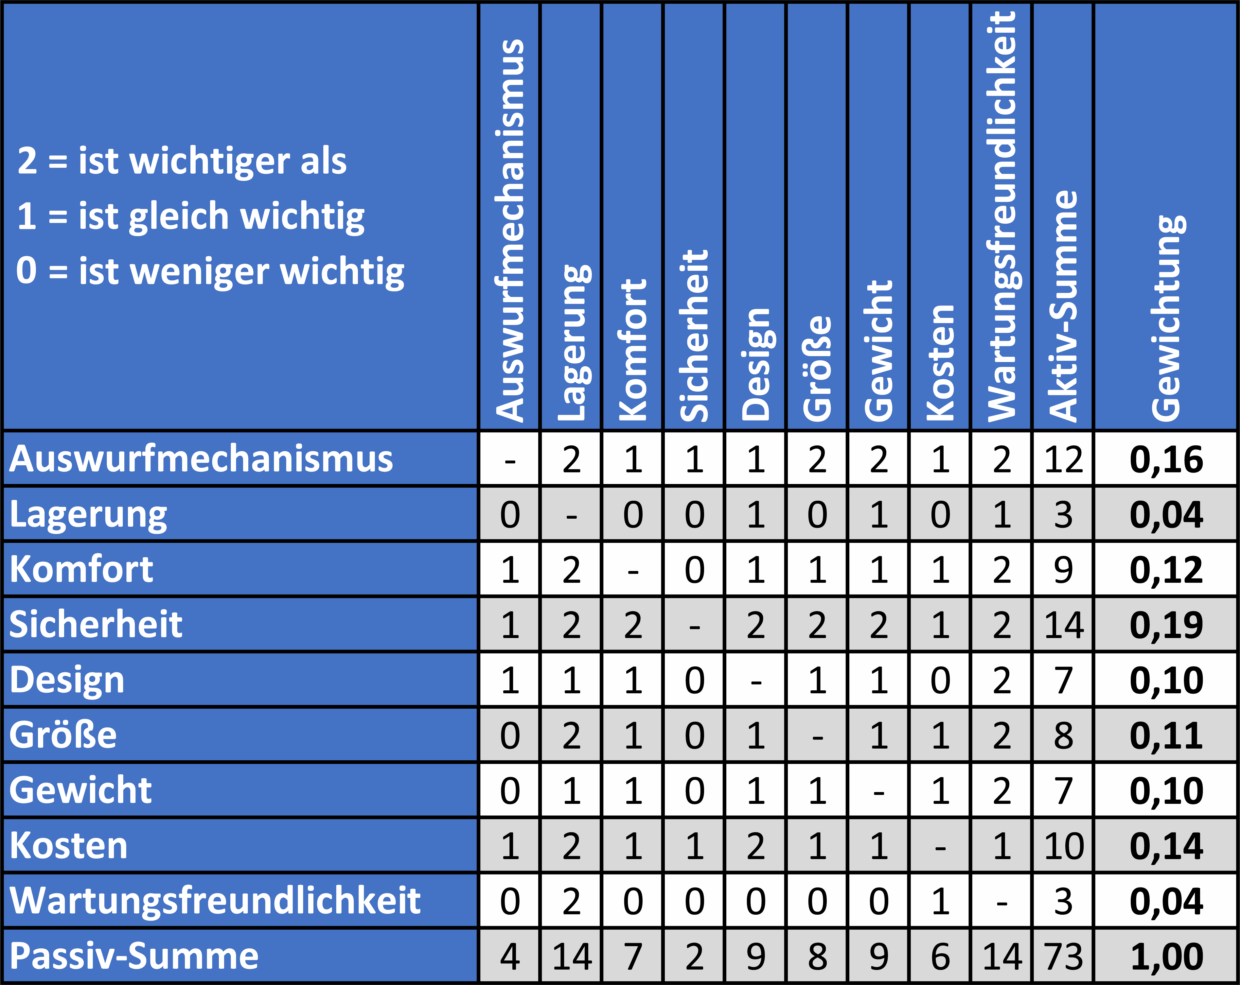
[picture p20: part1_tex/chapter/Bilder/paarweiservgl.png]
	
	\caption{Systematische Bestimmung der Gewichtungsfaktoren für die Bewertungskriterien durch den paarweisen Vergleich}
	\label{fig:paarweiservgl}
\end{figure}

\begin{figure}[H]
	\centering
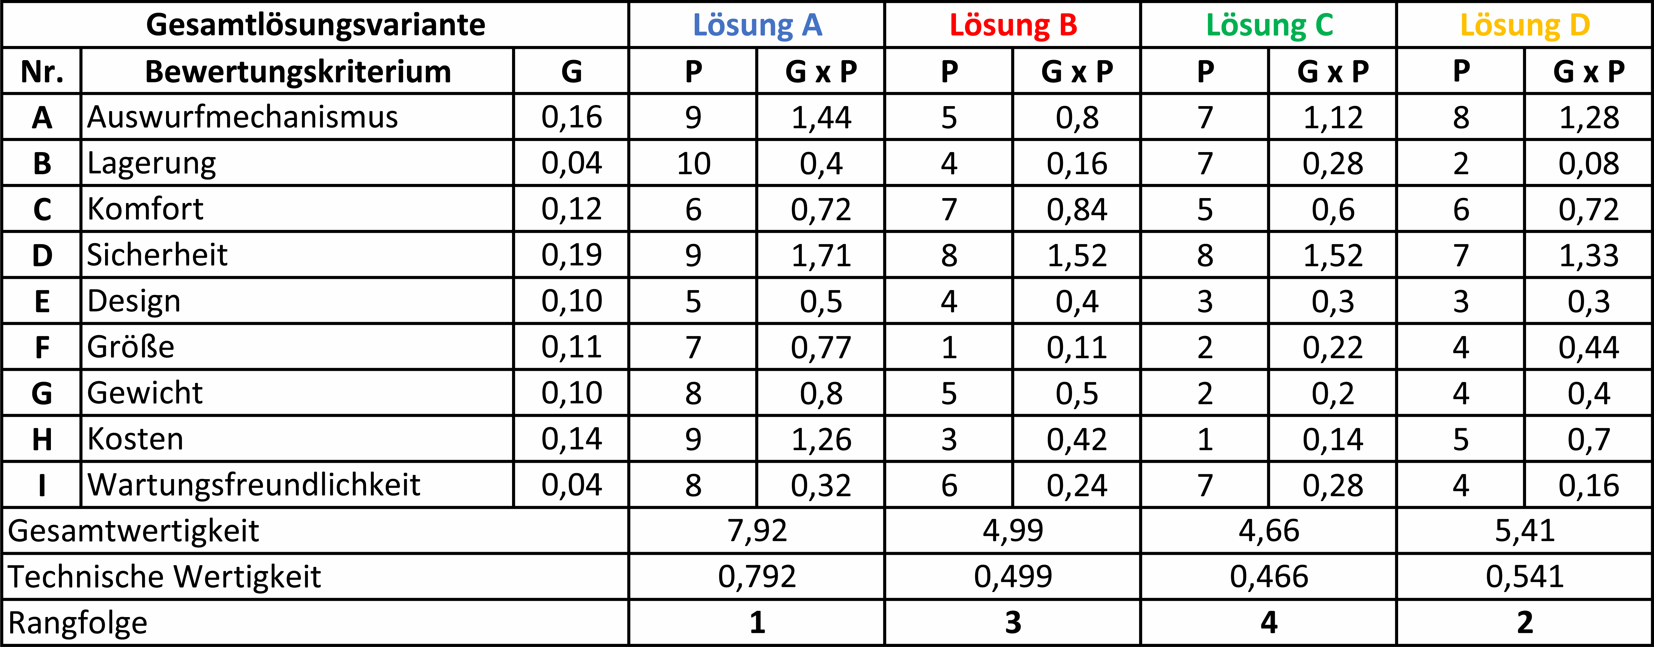
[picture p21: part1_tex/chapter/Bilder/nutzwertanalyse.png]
	
	\caption{Nutzwertanalyse zur Bewertung der Gesamtlösungskombinationen}
	\label{fig:nutzwertanalyse}
\end{figure}

\newpage
\section{Technische Prinzipskizze}

\begin{figure}[H]
	\centering
	
	\caption{Technische Funktionsskizze (links Vorderansicht, rechts Seitenansicht)}
	\label{fig:schematicbw}
\end{figure}

Diese technische Funktionsskizze zeigt den geplanten Aufbau der Apparatur. Zentral zu sehen ist der Trinkbehälter, dessen Positionierung automatisch erkannt wird. Darunter befindet sich ein kleines Display, worauf wichtige Informationen anzeigt werden. Über dem Trinkbehälter liegt das Herzstück der Konstruktion, die Vitamintabletten mit einem servogesteuerten, automatischen Auswurfmechanismus.

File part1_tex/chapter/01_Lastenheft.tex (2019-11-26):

% !TeX encoding = UTF-8
% !TeX root = ../Vitamintablettenspender.tex

\chapter{Lastenheft}

Es ist die Entwicklung eines innovativen Haushalt-Gadgets in AM-\&Multimaterial-Design vorgegeben. Dabei soll ein bedeutsames aber zeitgleich auch revolutionäres und innovatives Produkt entworfen werden. Vom Kunde ist ein Vitamintablettenspender gewünscht. Dieser soll über folgende Funktionen verfügen:

\begin{itemize}
	\item Aufbewahrungsmöglichkeit für mindestens zwei unterschiedliche Vitamintablettensorten
	\item Automatischer Tablettenauswurf in einen Trinkbehälter
	\item Handlich
	\item Leicht
\end{itemize}

Dazu wurden zusätzliche Kundenbefragungen und Umfragen hinsichtlich wünschenswerter Zusatzfunktionen durchgeführt. Als begeisternde Kriterien wurden folgende Wunschanforderungen formuliert:

\begin{itemize}
	\item Touchdisplay zur Bedienung
	\item Automatisches Auffüllen des Trinkbehälters mit Wasser
	\item Füllstandanzeige der Tablettenreservoirs
\end{itemize}

Das Produkt soll dem Kunden im Februar 2020 mittels einem fertigen Prototypen vorgestellt werden.

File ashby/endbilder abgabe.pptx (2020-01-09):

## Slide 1

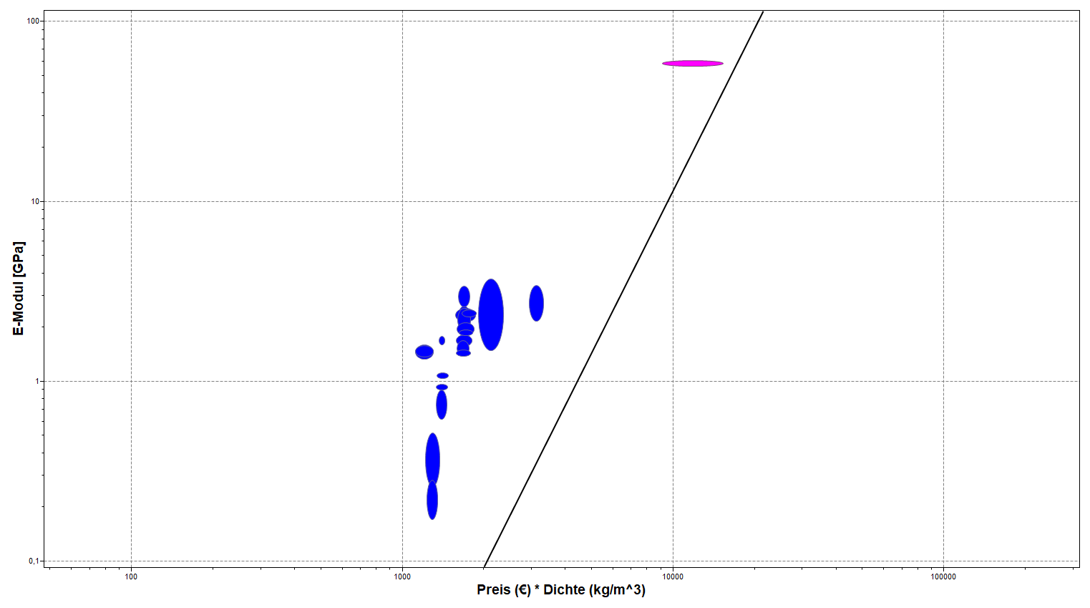
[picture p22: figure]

Natron- und kaligeschmelztes Glas

Polyvinylchlorid

Polypropylen

Polyethylen (HD)

Polyethylen (LD)

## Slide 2


Styrol-Acrylnitril

Polypropylen

Polystyrol

Acrylnitril-Butadien-Styrol

Polyethylen (HD)

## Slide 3


Aluminiumsilicate

Kali-Natron-Zink-Glas

Kalk-Natron-Glas

Low E-Glas

Natron-Zinkglas

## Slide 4


Polyesterfasern

Polyethylenterephthalat

Polypropylen

Polyethylen (MD)

Polyethylen (HD)

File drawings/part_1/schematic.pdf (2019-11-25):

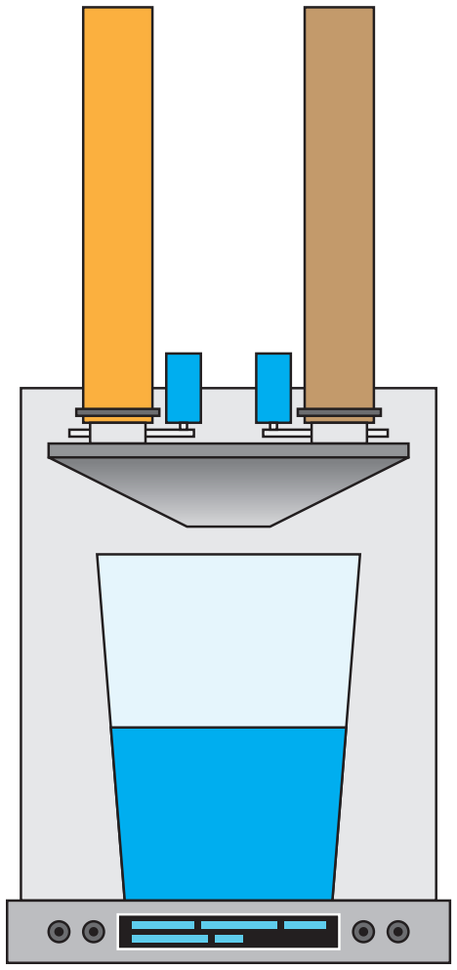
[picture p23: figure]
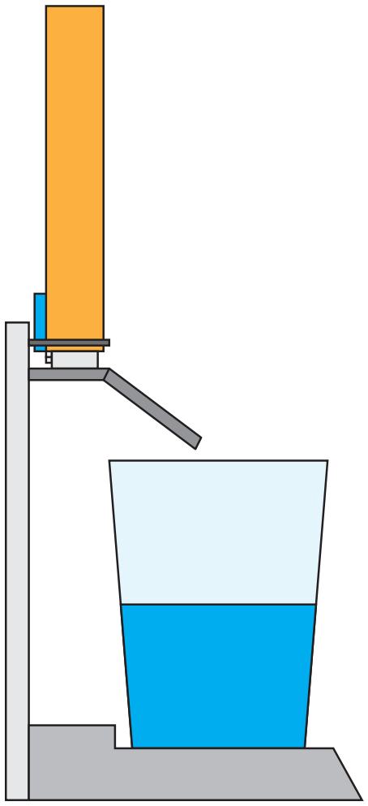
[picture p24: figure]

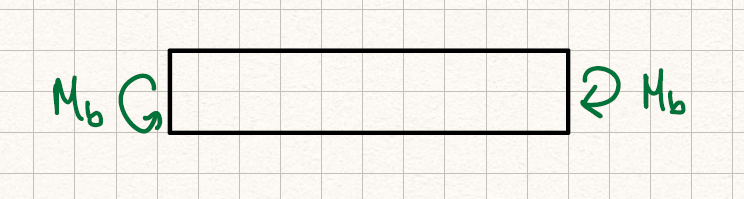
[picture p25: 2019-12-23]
part1_tex/chapter/Bilder/0301modell.png

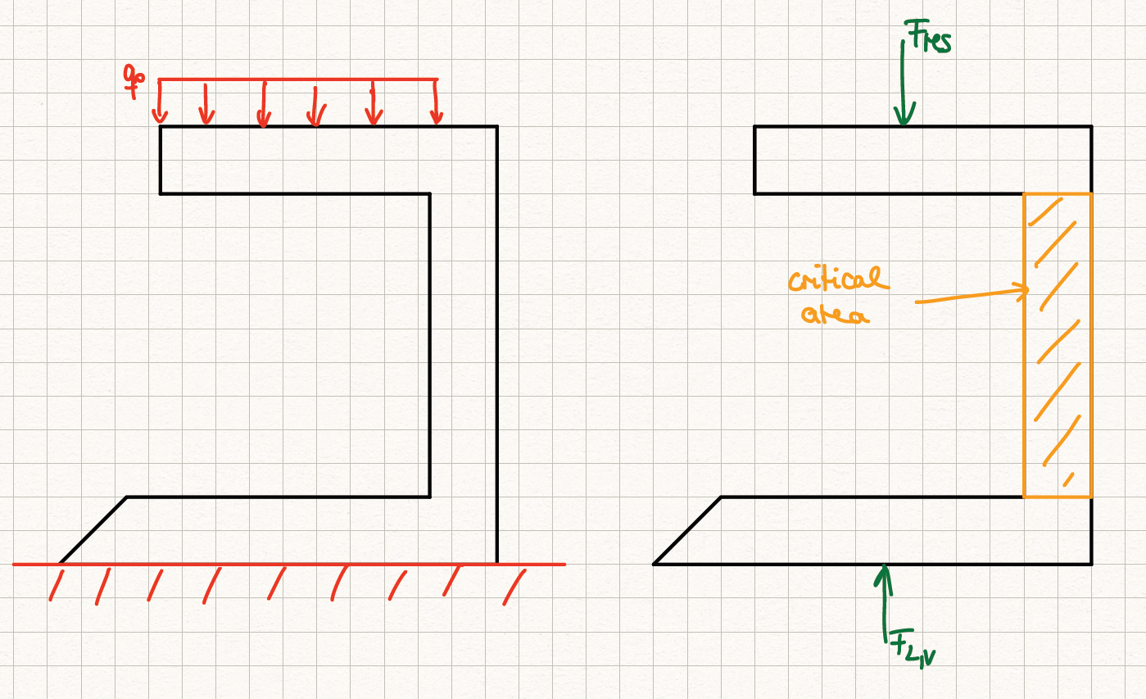
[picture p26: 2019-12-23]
part1_tex/chapter/Bilder/0301skizze.png

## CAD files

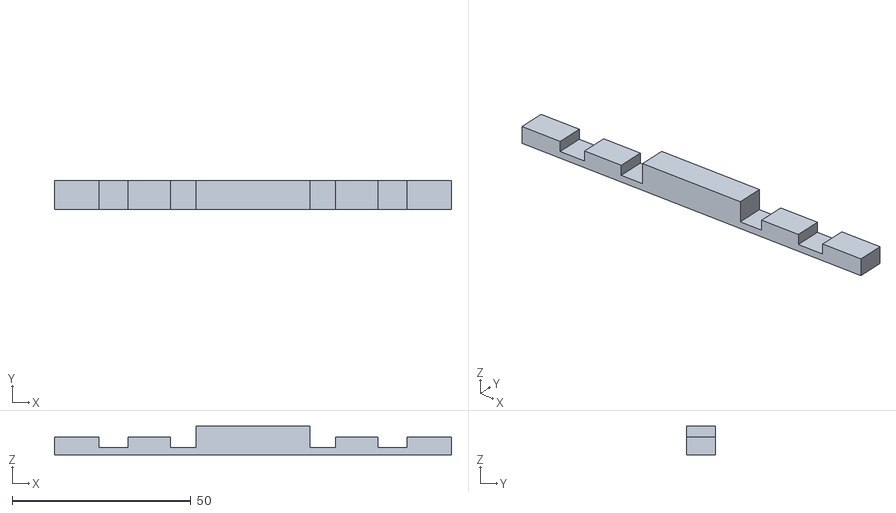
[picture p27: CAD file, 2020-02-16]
3d druck stl/01_Gehäuseboden/01_gehaeuseboden_halter_elektronik.stl
111.0 x 8.00 x 8.00

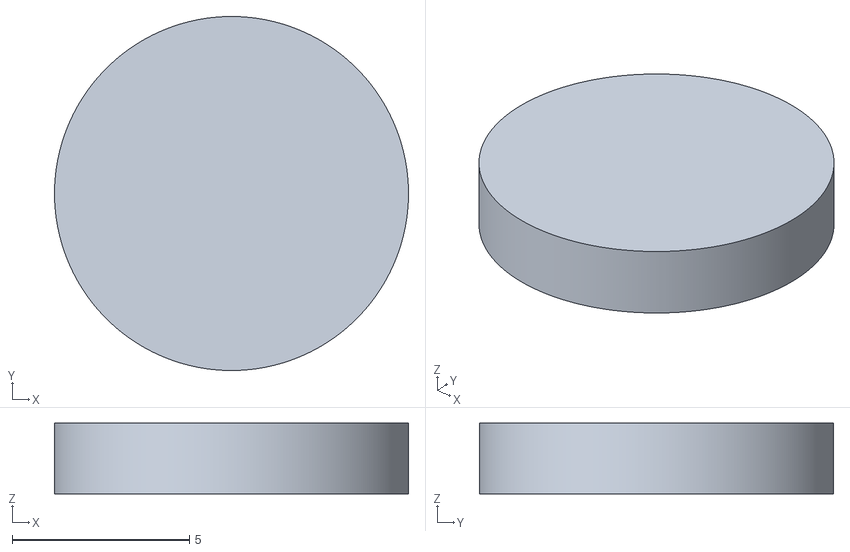
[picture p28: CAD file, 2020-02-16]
3d druck stl/01_Trinkbehälterauflage/01_trinkbehaelterauflage_1.stl
10.0 x 10.0 x 2.00

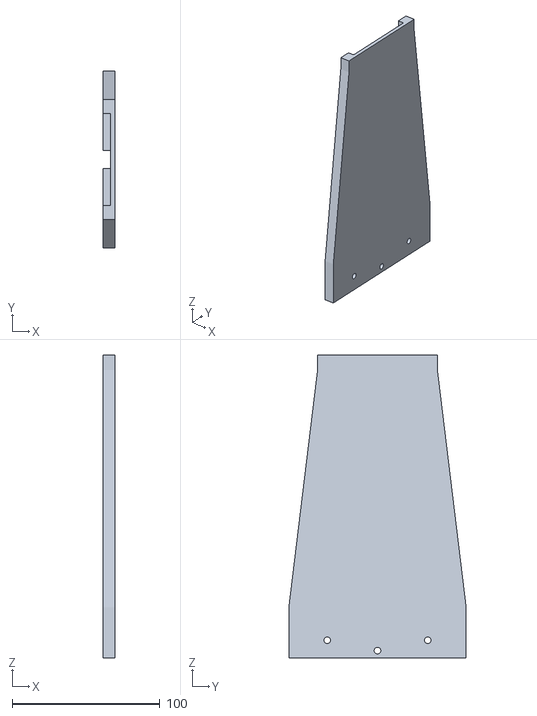
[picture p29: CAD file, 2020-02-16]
3d druck stl/02_Gehäuserückwand_teil1/02_gehaeuserueckwand.stl
8.00 x 120.0 x 205.0

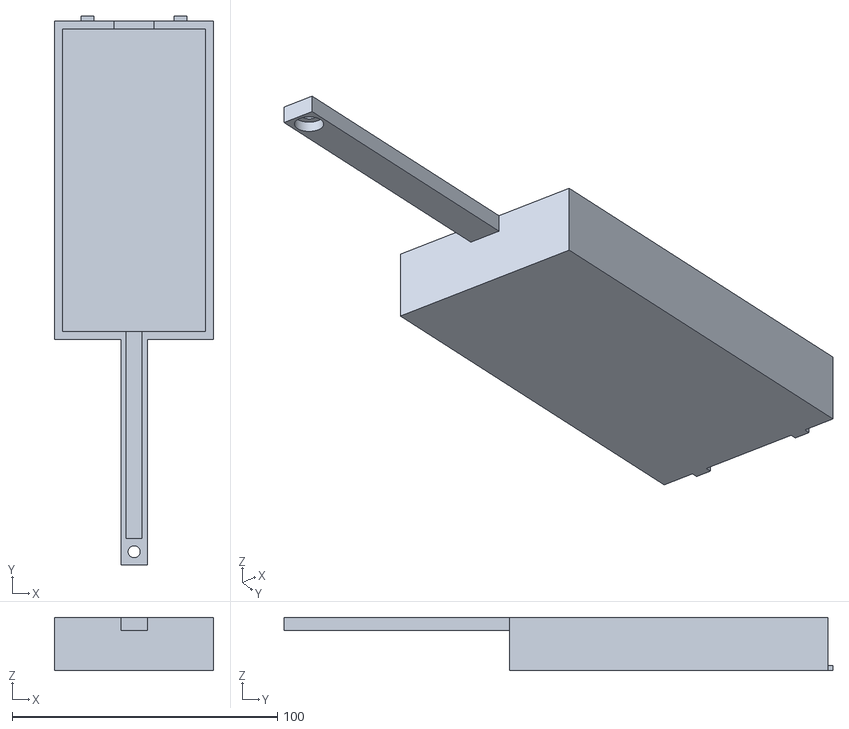
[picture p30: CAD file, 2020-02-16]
3d druck stl/02_Gehäuserückwand_teil2/02_gehaeuserueckwand_2_platte.stl
60.0 x 206.9 x 20.0

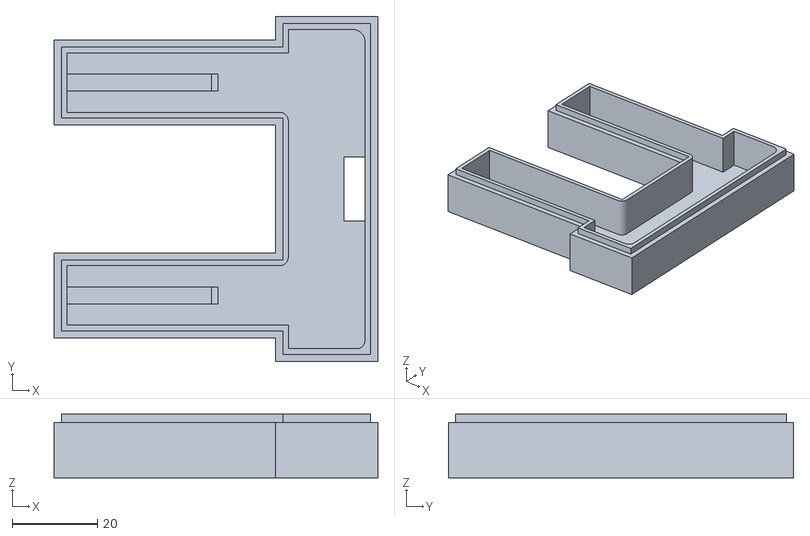
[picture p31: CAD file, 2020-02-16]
3d druck stl/02_Gehäuserückwand_teil3/02_gehaeuserueckwand_3.stl
76.0 x 81.0 x 15.0

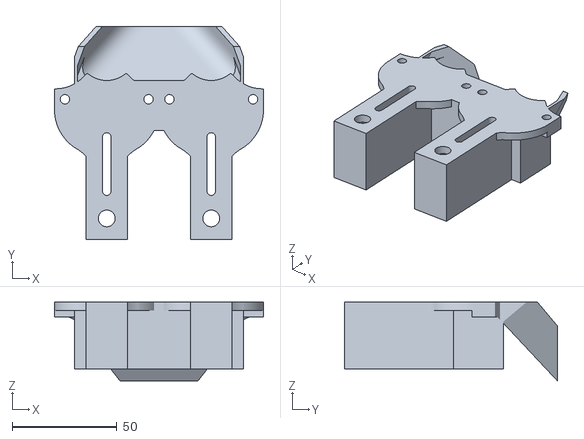
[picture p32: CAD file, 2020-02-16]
3d druck stl/03_Tablettenrutsche/03_tablettenrutsche.stl
100.0 x 101.7 x 37.6

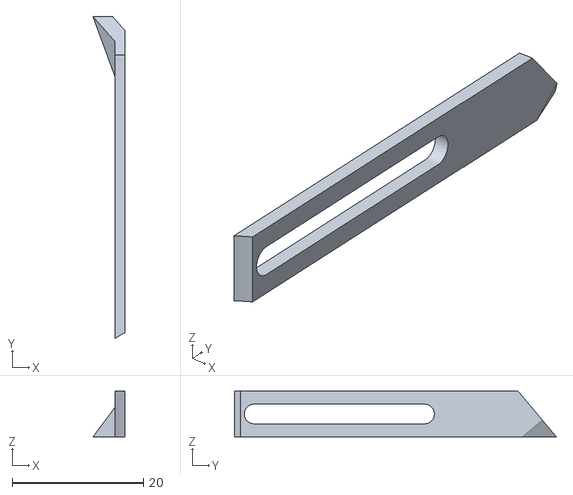
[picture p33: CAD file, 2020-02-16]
3d druck stl/03_Tablettenrutsche_Führungsteile/03_tablettenrutsche_führung_R.stl
4.92 x 49.1 x 7.00

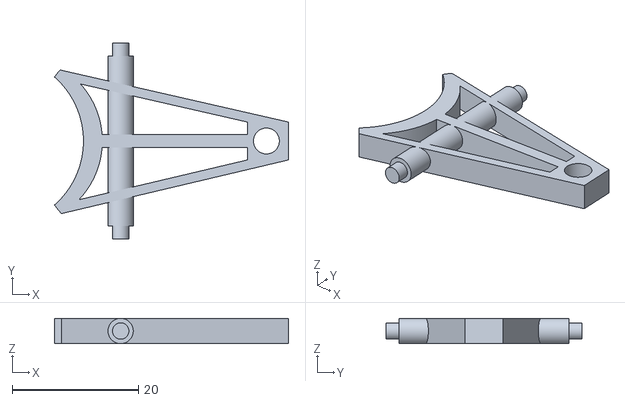
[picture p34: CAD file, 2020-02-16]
3d druck stl/04_Aktoren/04_schieber.stl
37.1 x 31.0 x 4.00

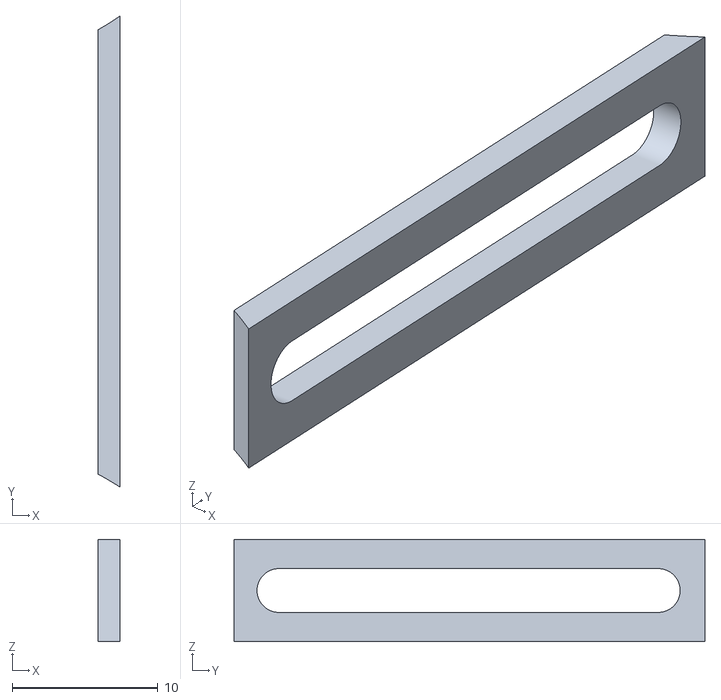
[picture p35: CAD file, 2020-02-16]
3d druck stl/03_Tablettenrutsche_Führungsteile/03_tablettenrutsche_IR.stl
1.50 x 32.3 x 7.00

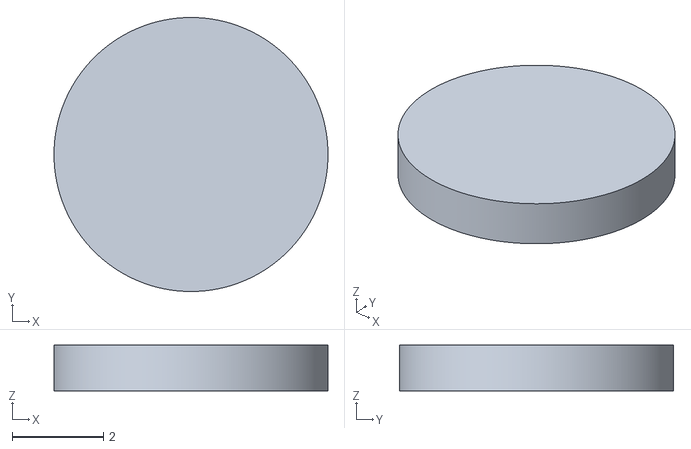
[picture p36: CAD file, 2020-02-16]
3d druck stl/04_Aktoren/04_pleuel2_stopper.stl
6.00 x 6.00 x 1.00

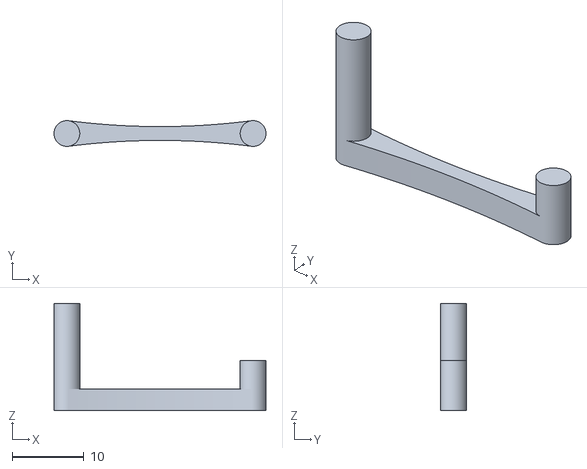
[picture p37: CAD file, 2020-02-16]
3d druck stl/04_Aktoren/04_pleuel2.stl
29.6 x 3.60 x 15.0

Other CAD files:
3d druck stl/03_Tablettenrutsche_Führungsteile/03_tablettenrutsche_führung_L.stl
3d druck stl/03_Tablettenrutsche_Führungsteile/03_tablettenrutsche_IL.stl
CAD_drawings/00_vitamintablettenspender_zusammenbau.prt
CAD_drawings/00_vitamintablettenspender_zusammenbau_dimetrisch.prt
CAD_drawings/01_gehaeuseboden.prt
CAD_drawings/01_gehaeuseboden_halter_elektronik.prt
CAD_drawings/01_trinkbehaelterauflage.prt
CAD_drawings/02_gehaeuserueckwand.prt
CAD_drawings/02_gehaeuserueckwand_platte.prt
CAD_drawings/03_tablettenrutsche.prt
CAD_drawings/04_pleuel1.prt
CAD_drawings/04_pleuel2.prt
CAD_drawings/04_schieber.prt
CAD_drawings/05_lagerung.prt
CAD_drawings/05_lagerung_deckel.prt
CAD_modelling/00_vitamintablettenspender_zusammenbau.prt
CAD_modelling/01_gehaeuseboden.prt
CAD_modelling/01_gehaeuseboden_halter_elektronik.prt
CAD_modelling/01_trinkbehaelterauflage.prt
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

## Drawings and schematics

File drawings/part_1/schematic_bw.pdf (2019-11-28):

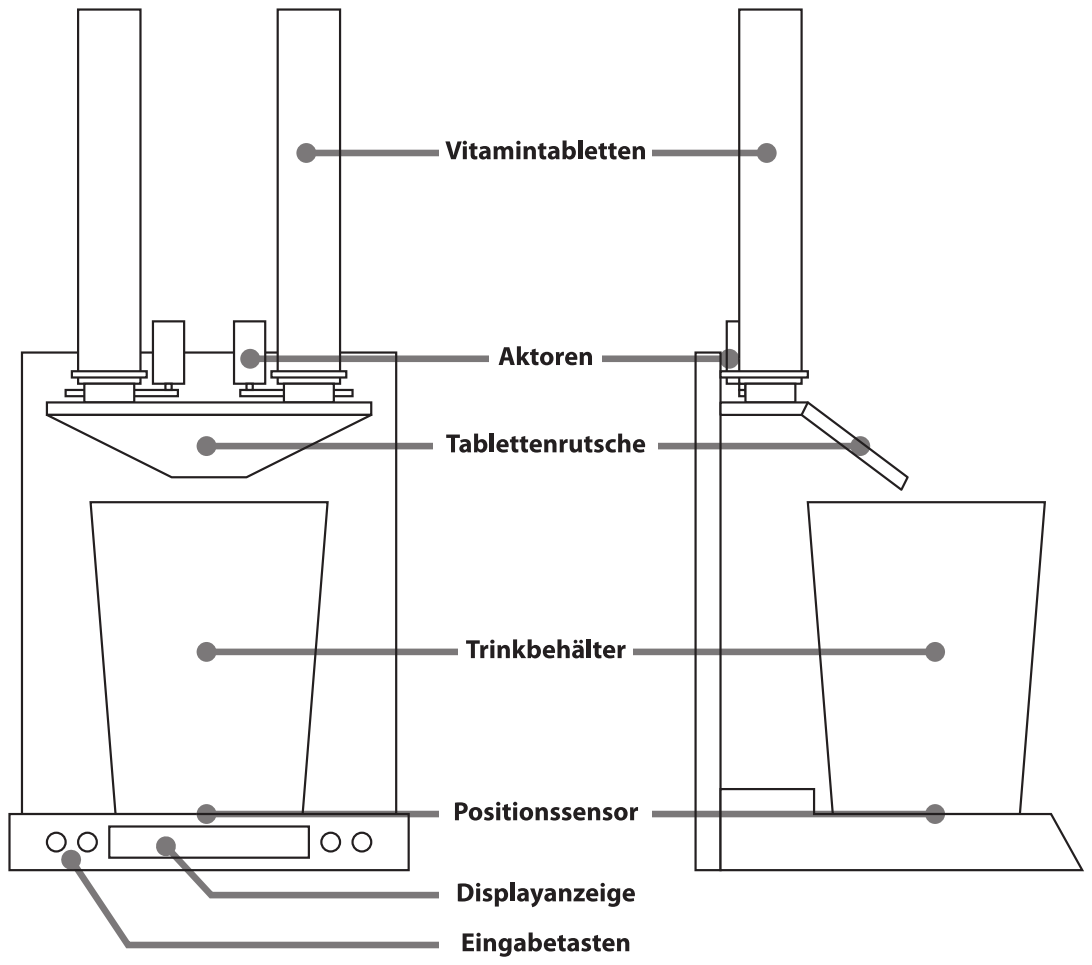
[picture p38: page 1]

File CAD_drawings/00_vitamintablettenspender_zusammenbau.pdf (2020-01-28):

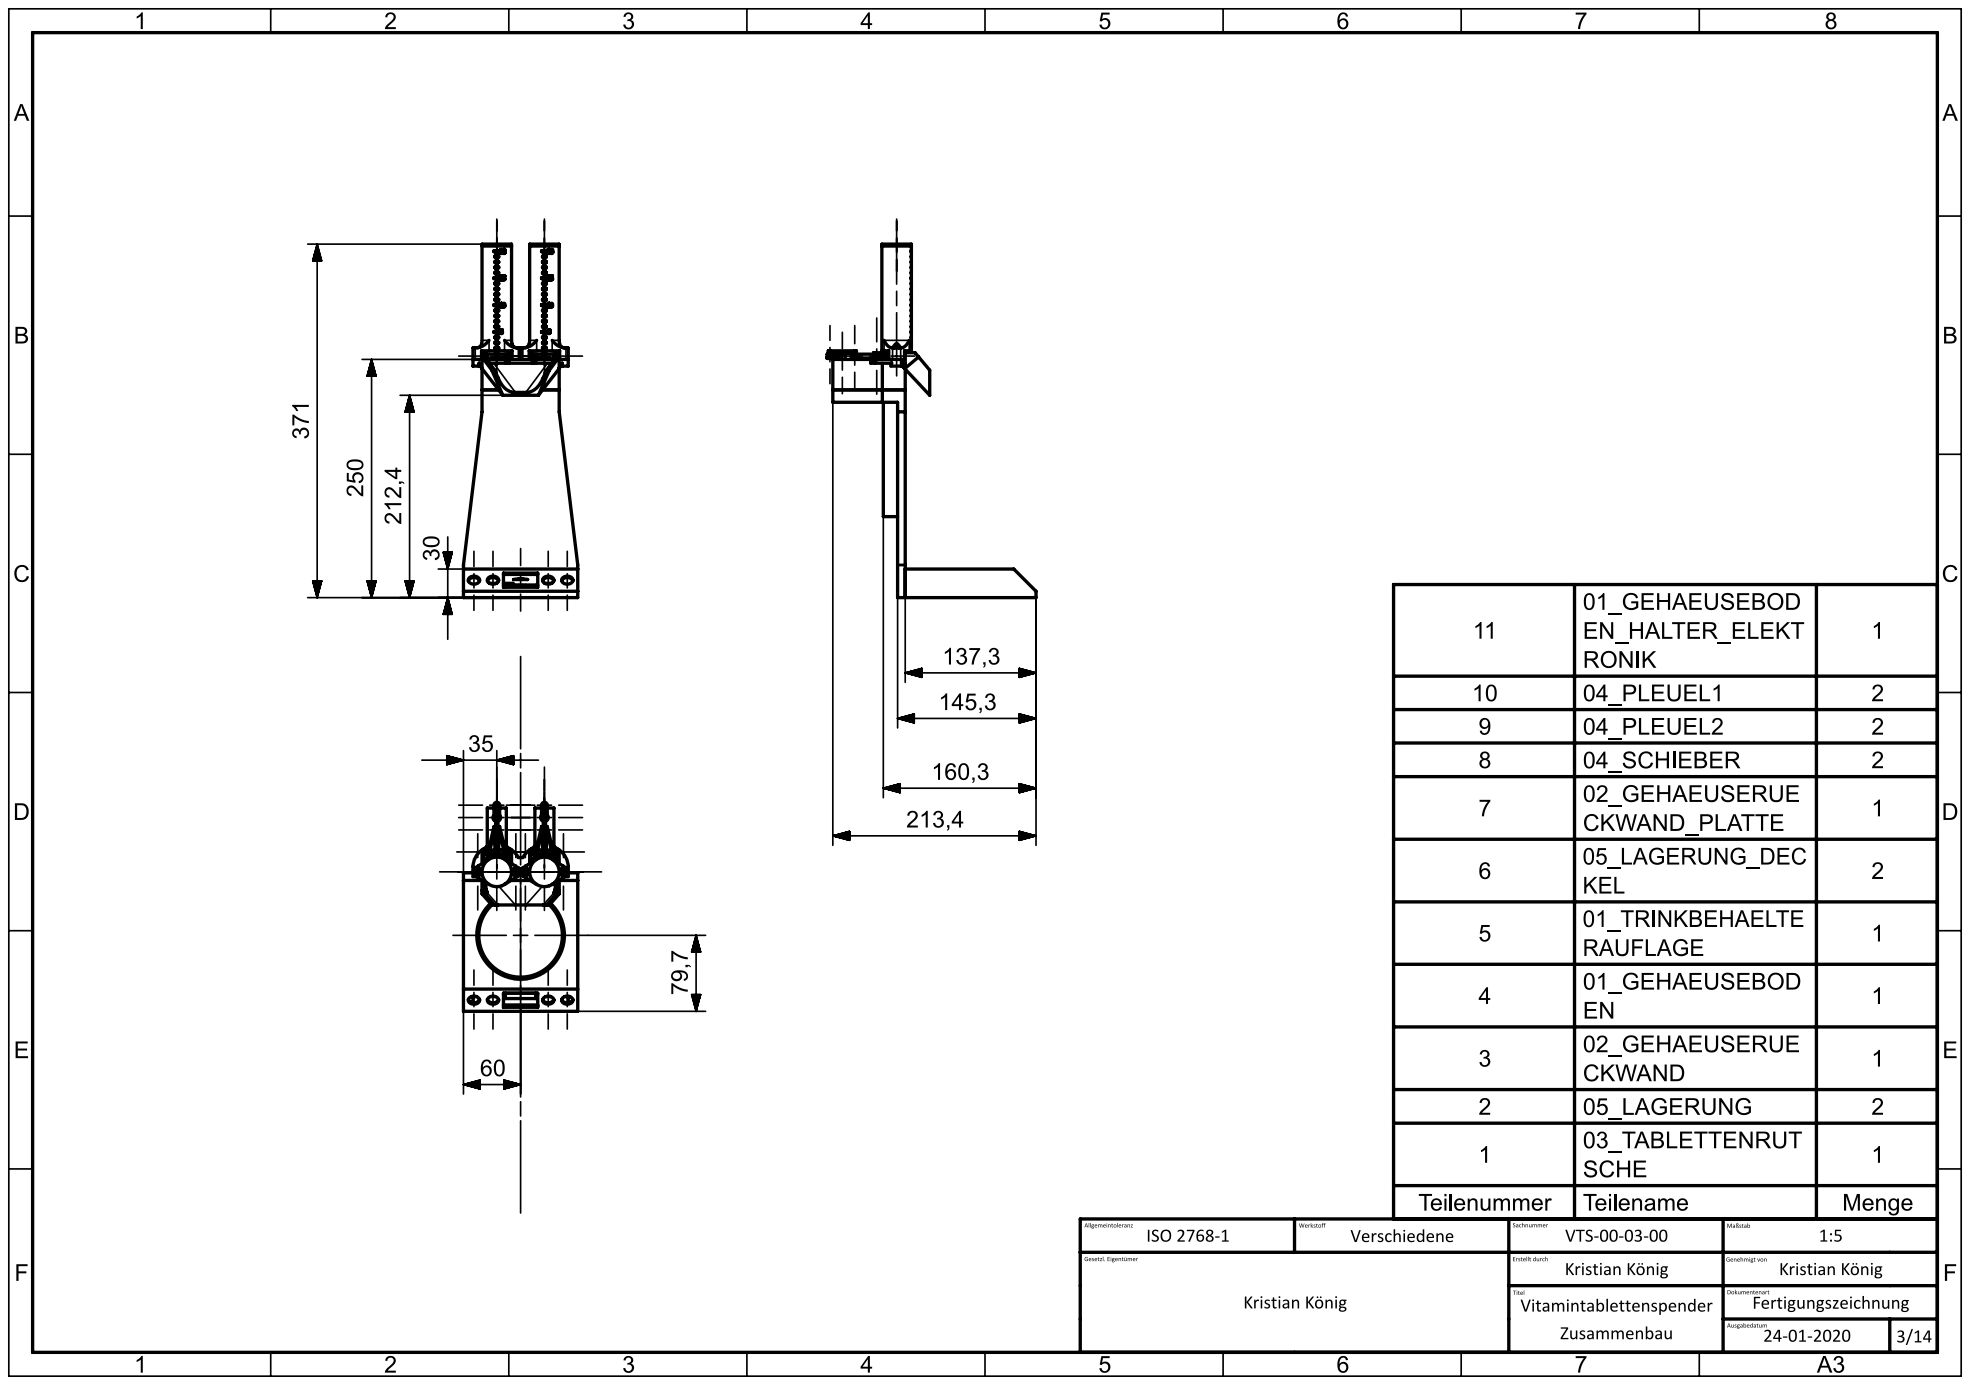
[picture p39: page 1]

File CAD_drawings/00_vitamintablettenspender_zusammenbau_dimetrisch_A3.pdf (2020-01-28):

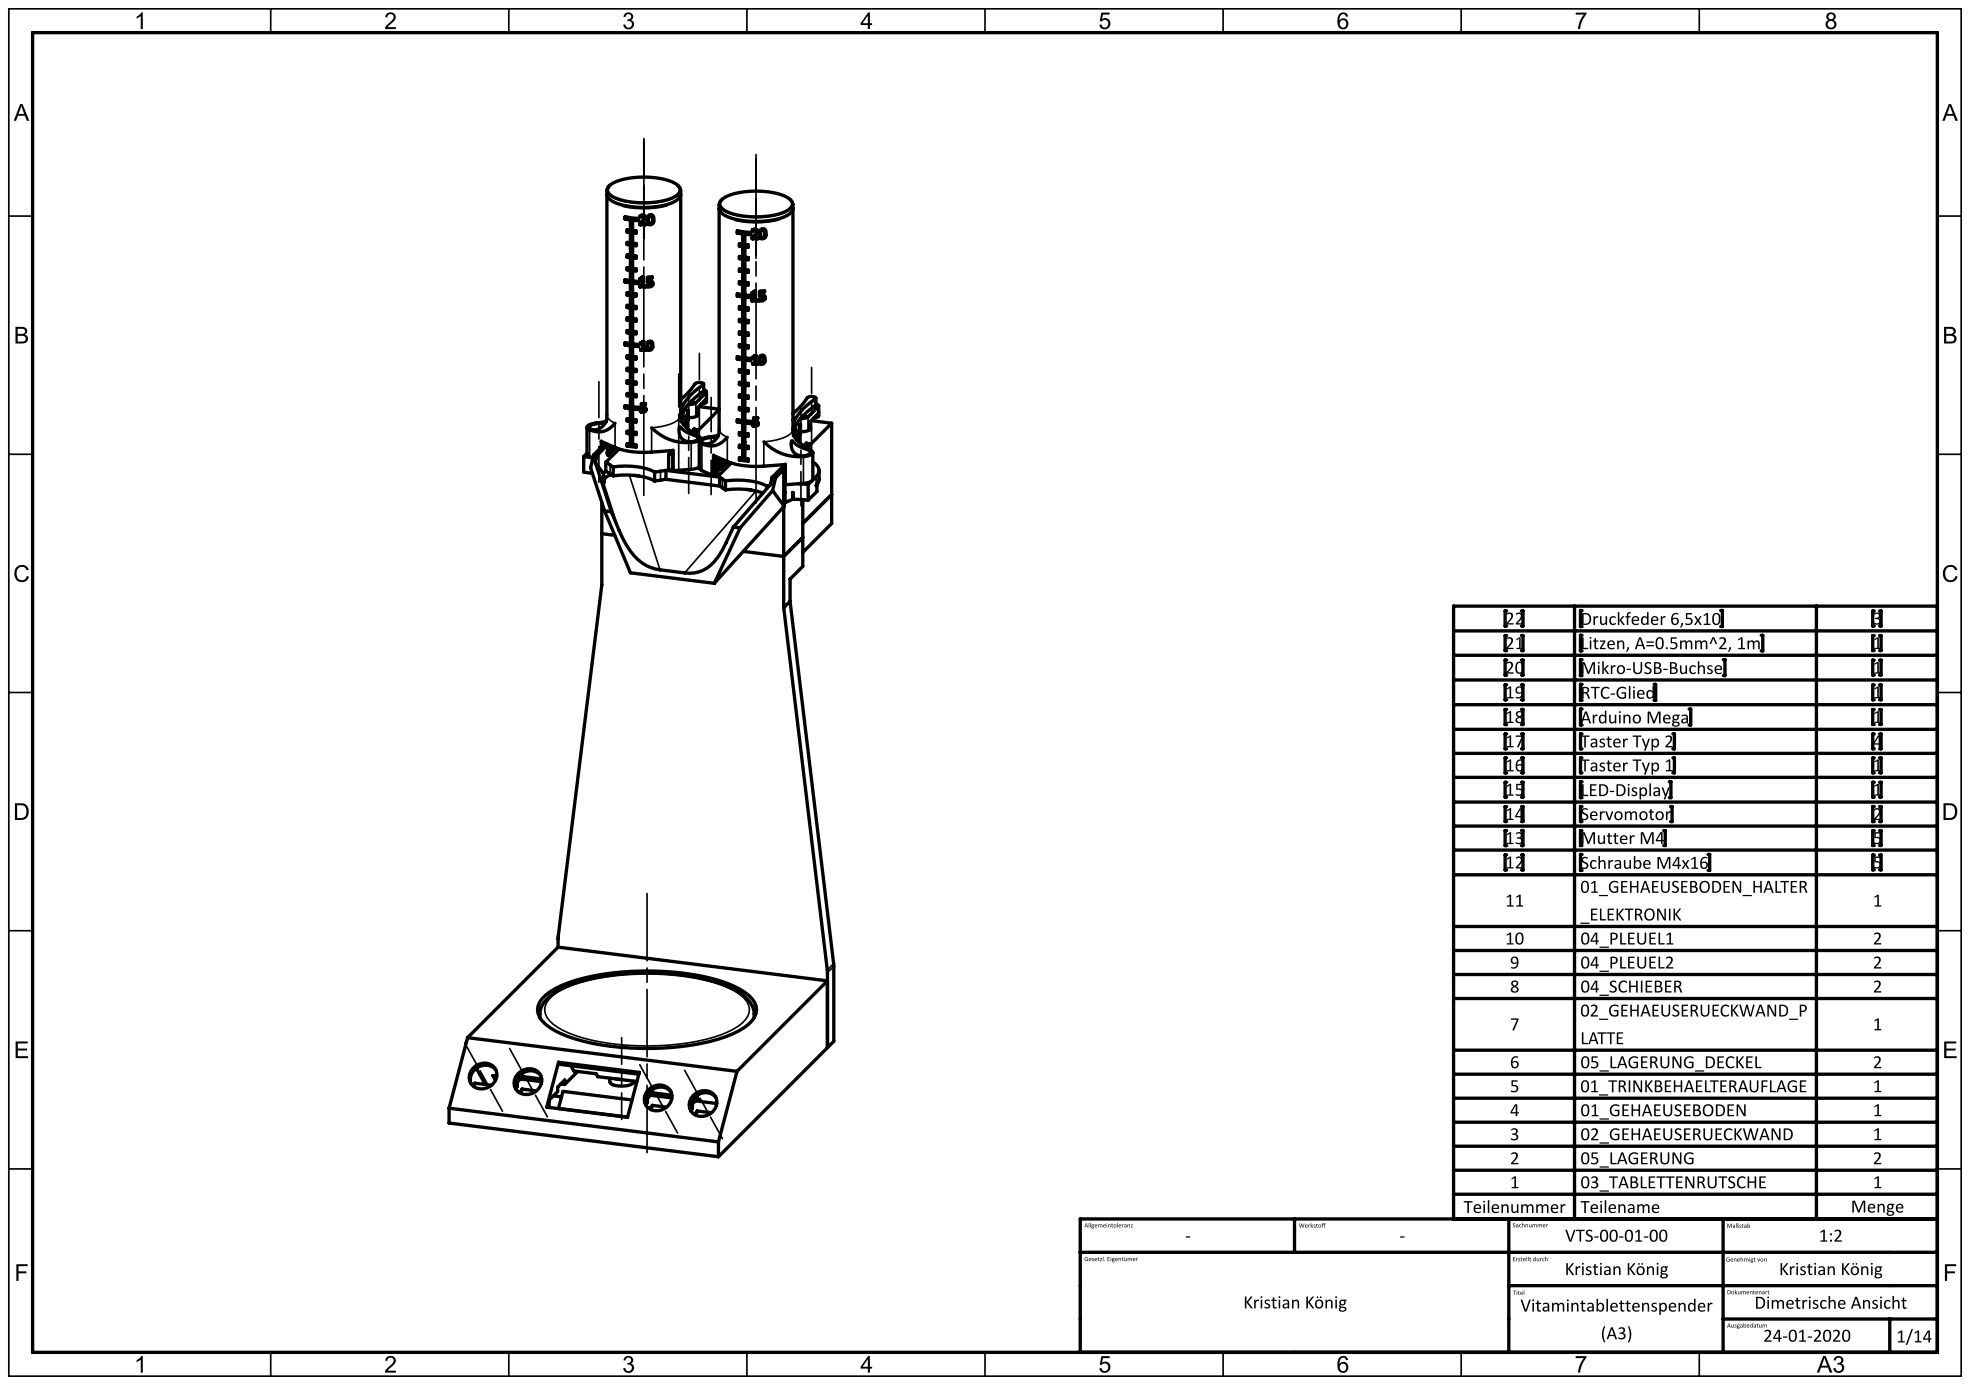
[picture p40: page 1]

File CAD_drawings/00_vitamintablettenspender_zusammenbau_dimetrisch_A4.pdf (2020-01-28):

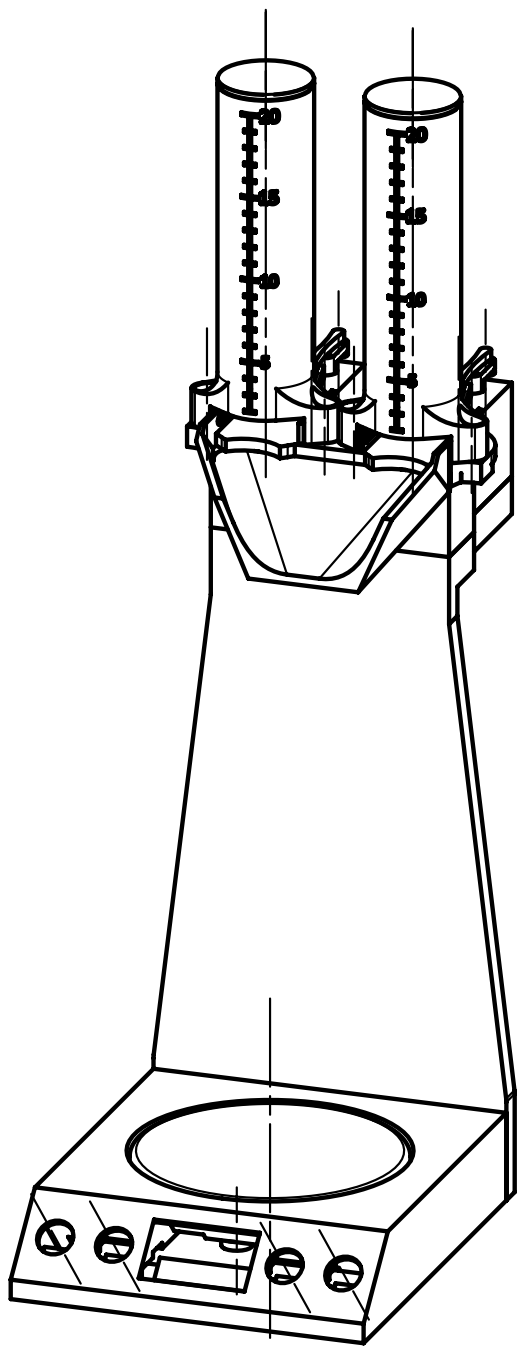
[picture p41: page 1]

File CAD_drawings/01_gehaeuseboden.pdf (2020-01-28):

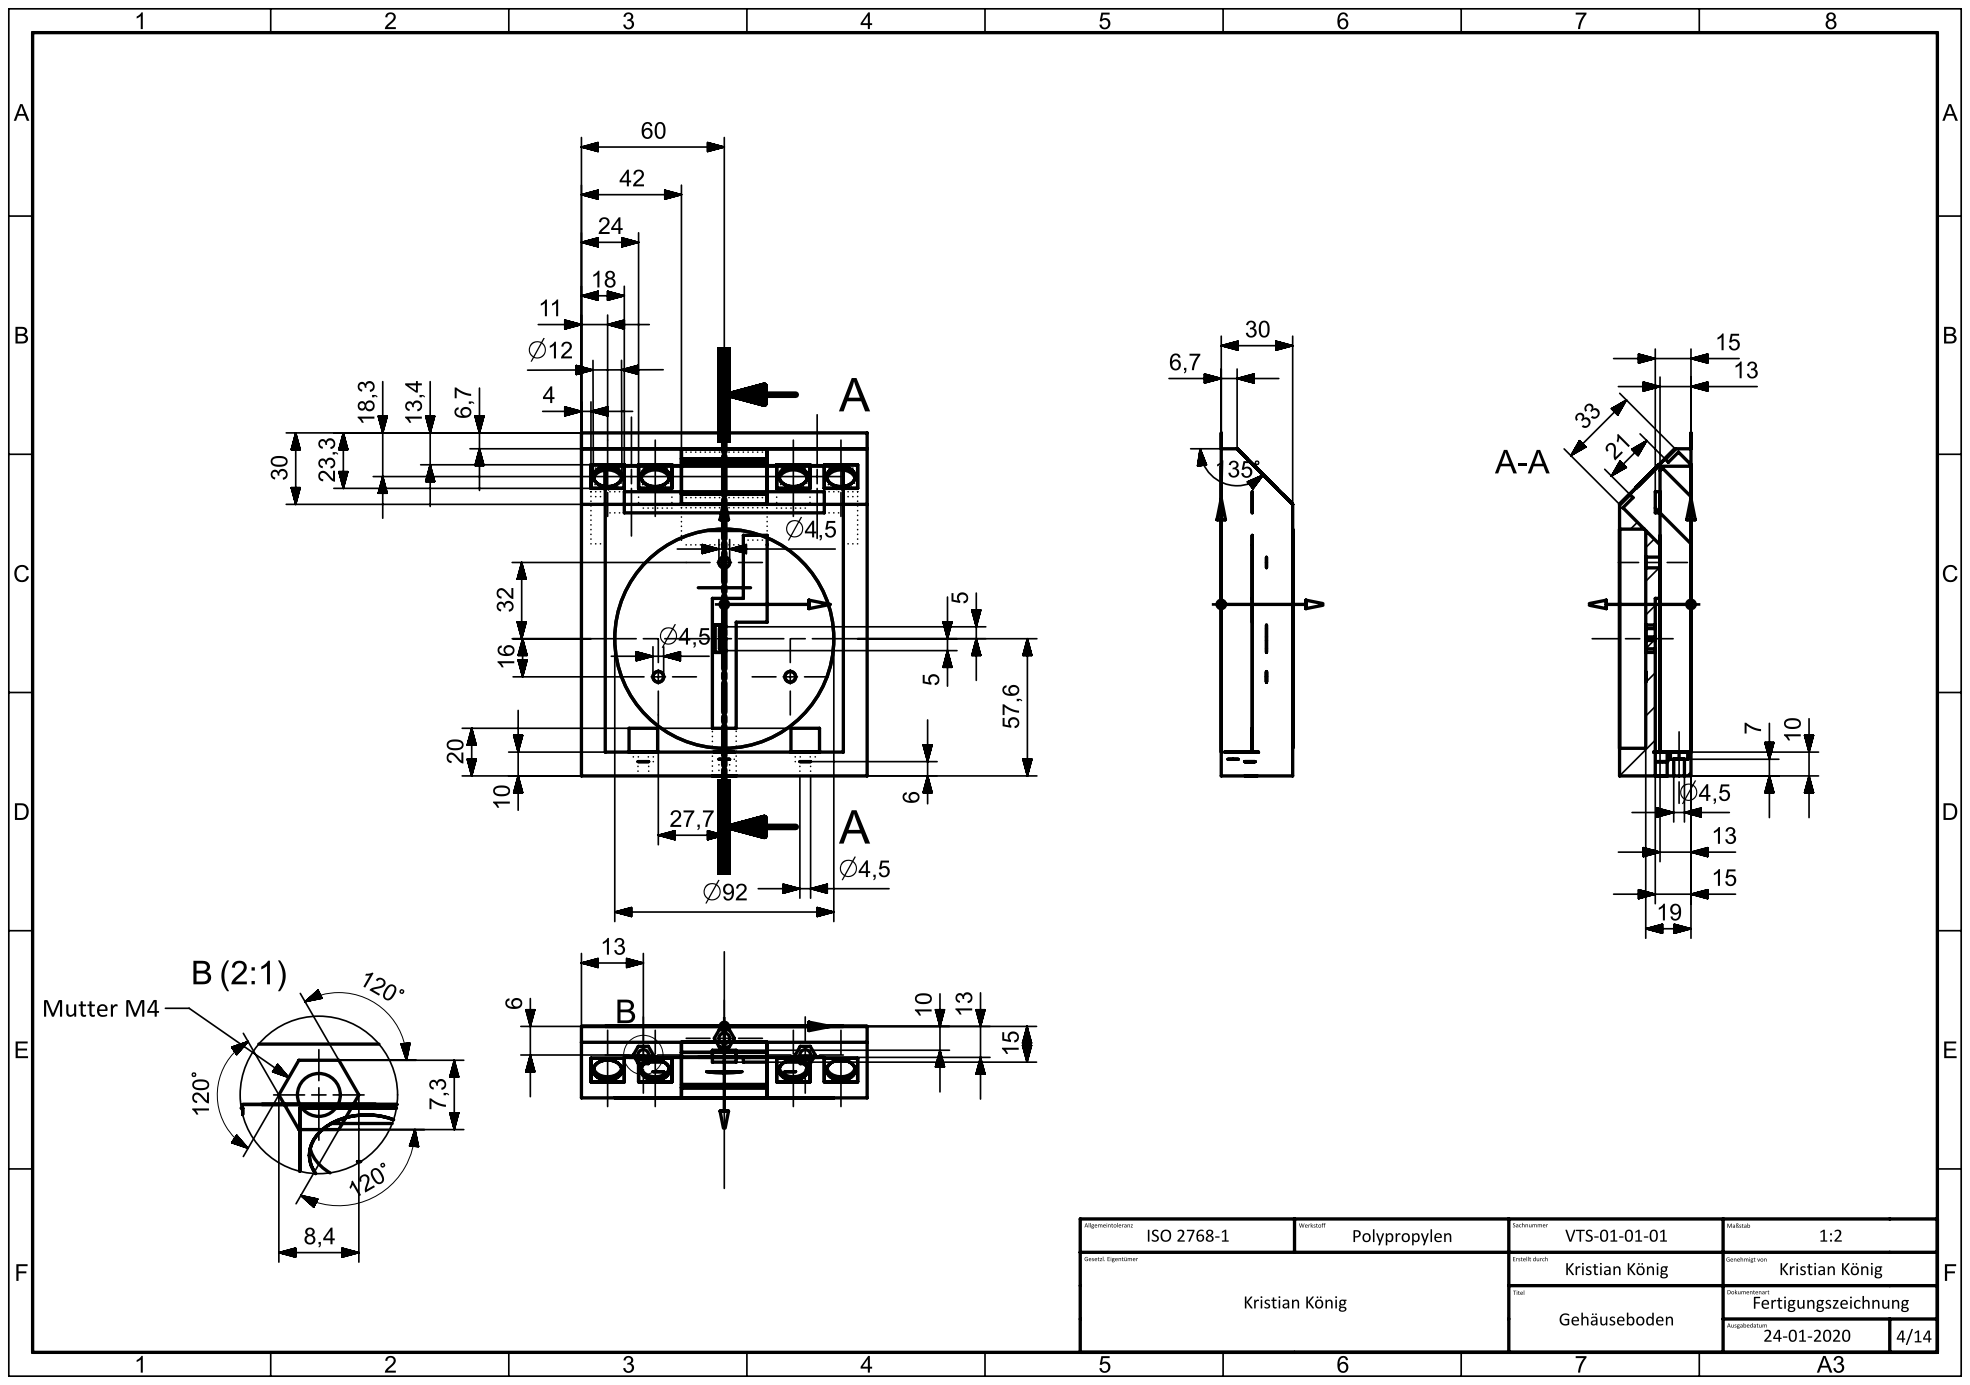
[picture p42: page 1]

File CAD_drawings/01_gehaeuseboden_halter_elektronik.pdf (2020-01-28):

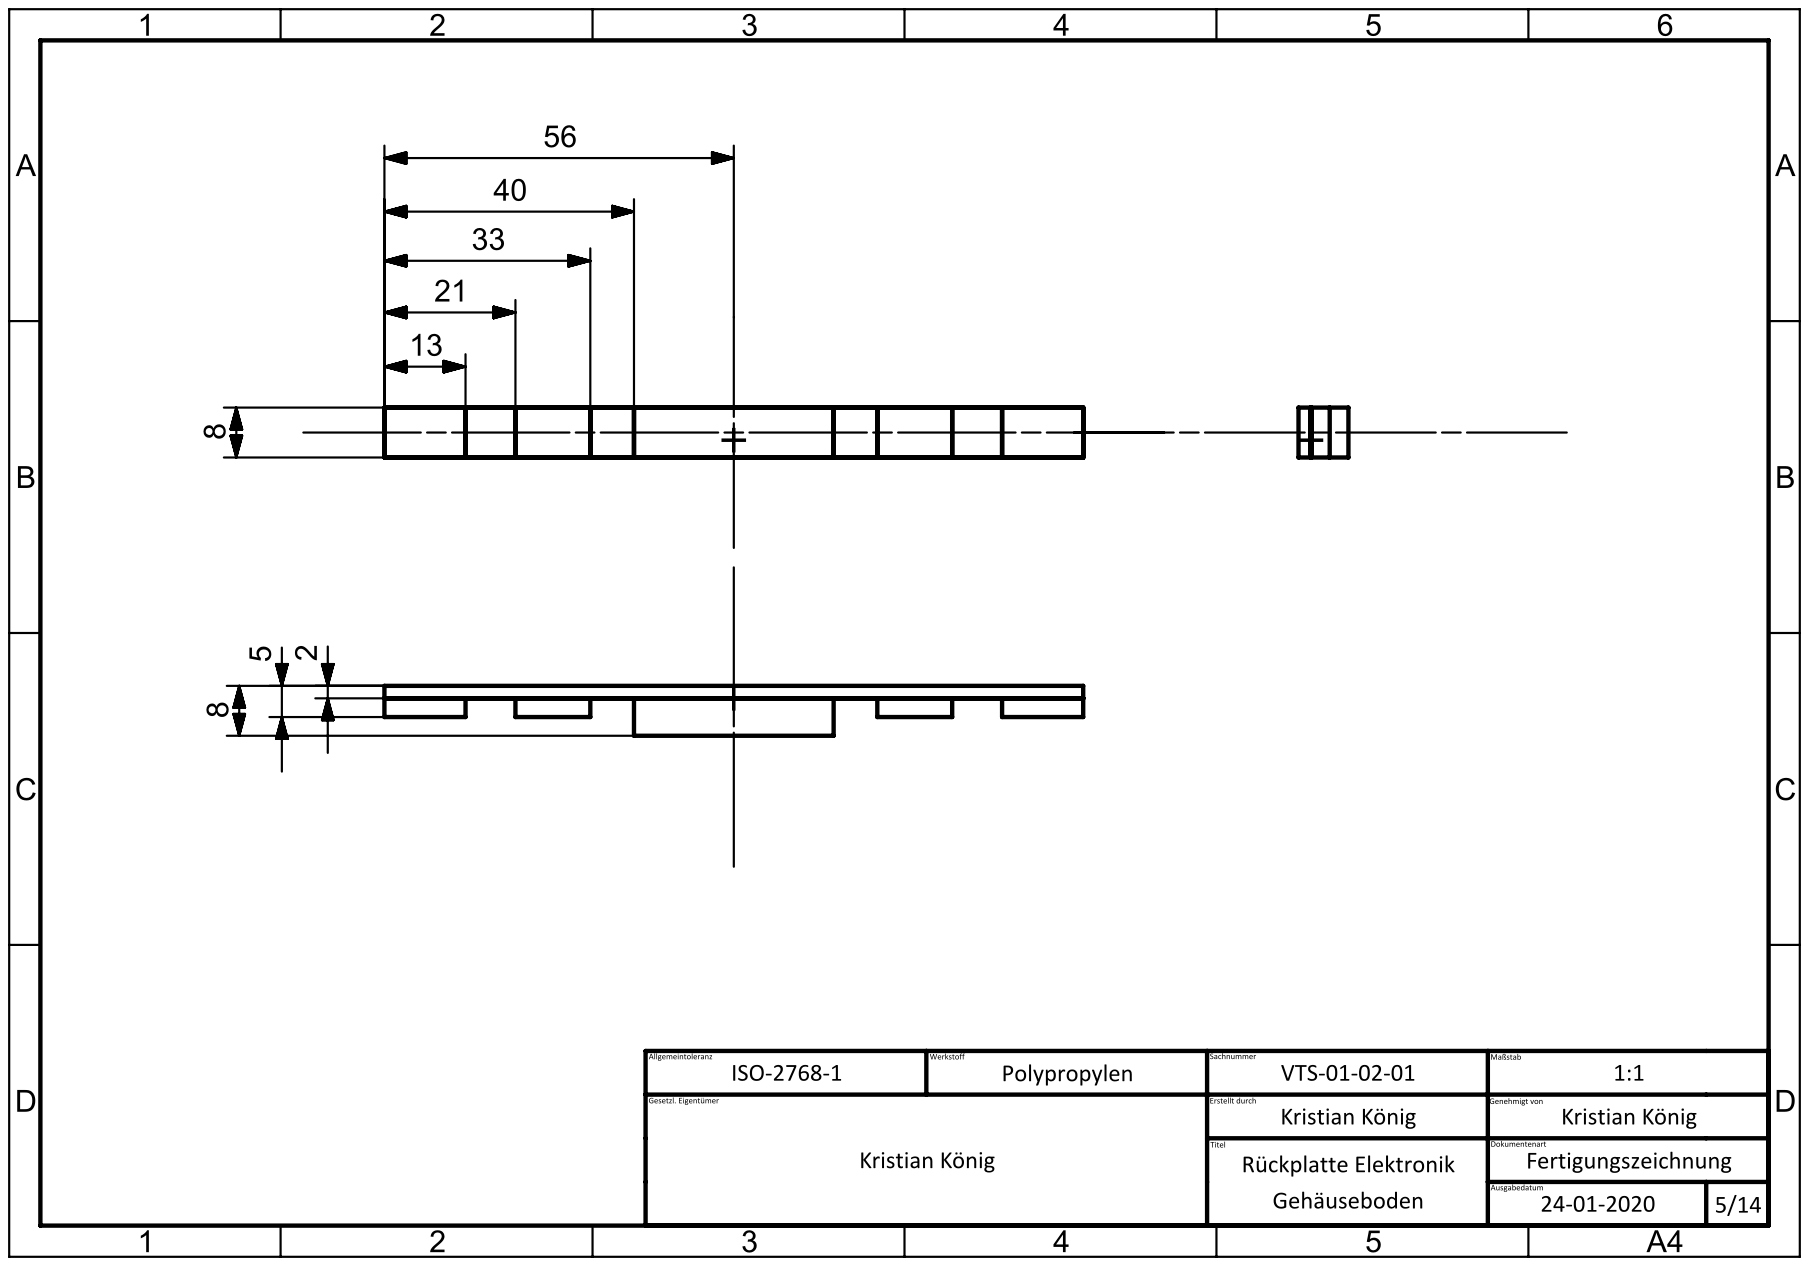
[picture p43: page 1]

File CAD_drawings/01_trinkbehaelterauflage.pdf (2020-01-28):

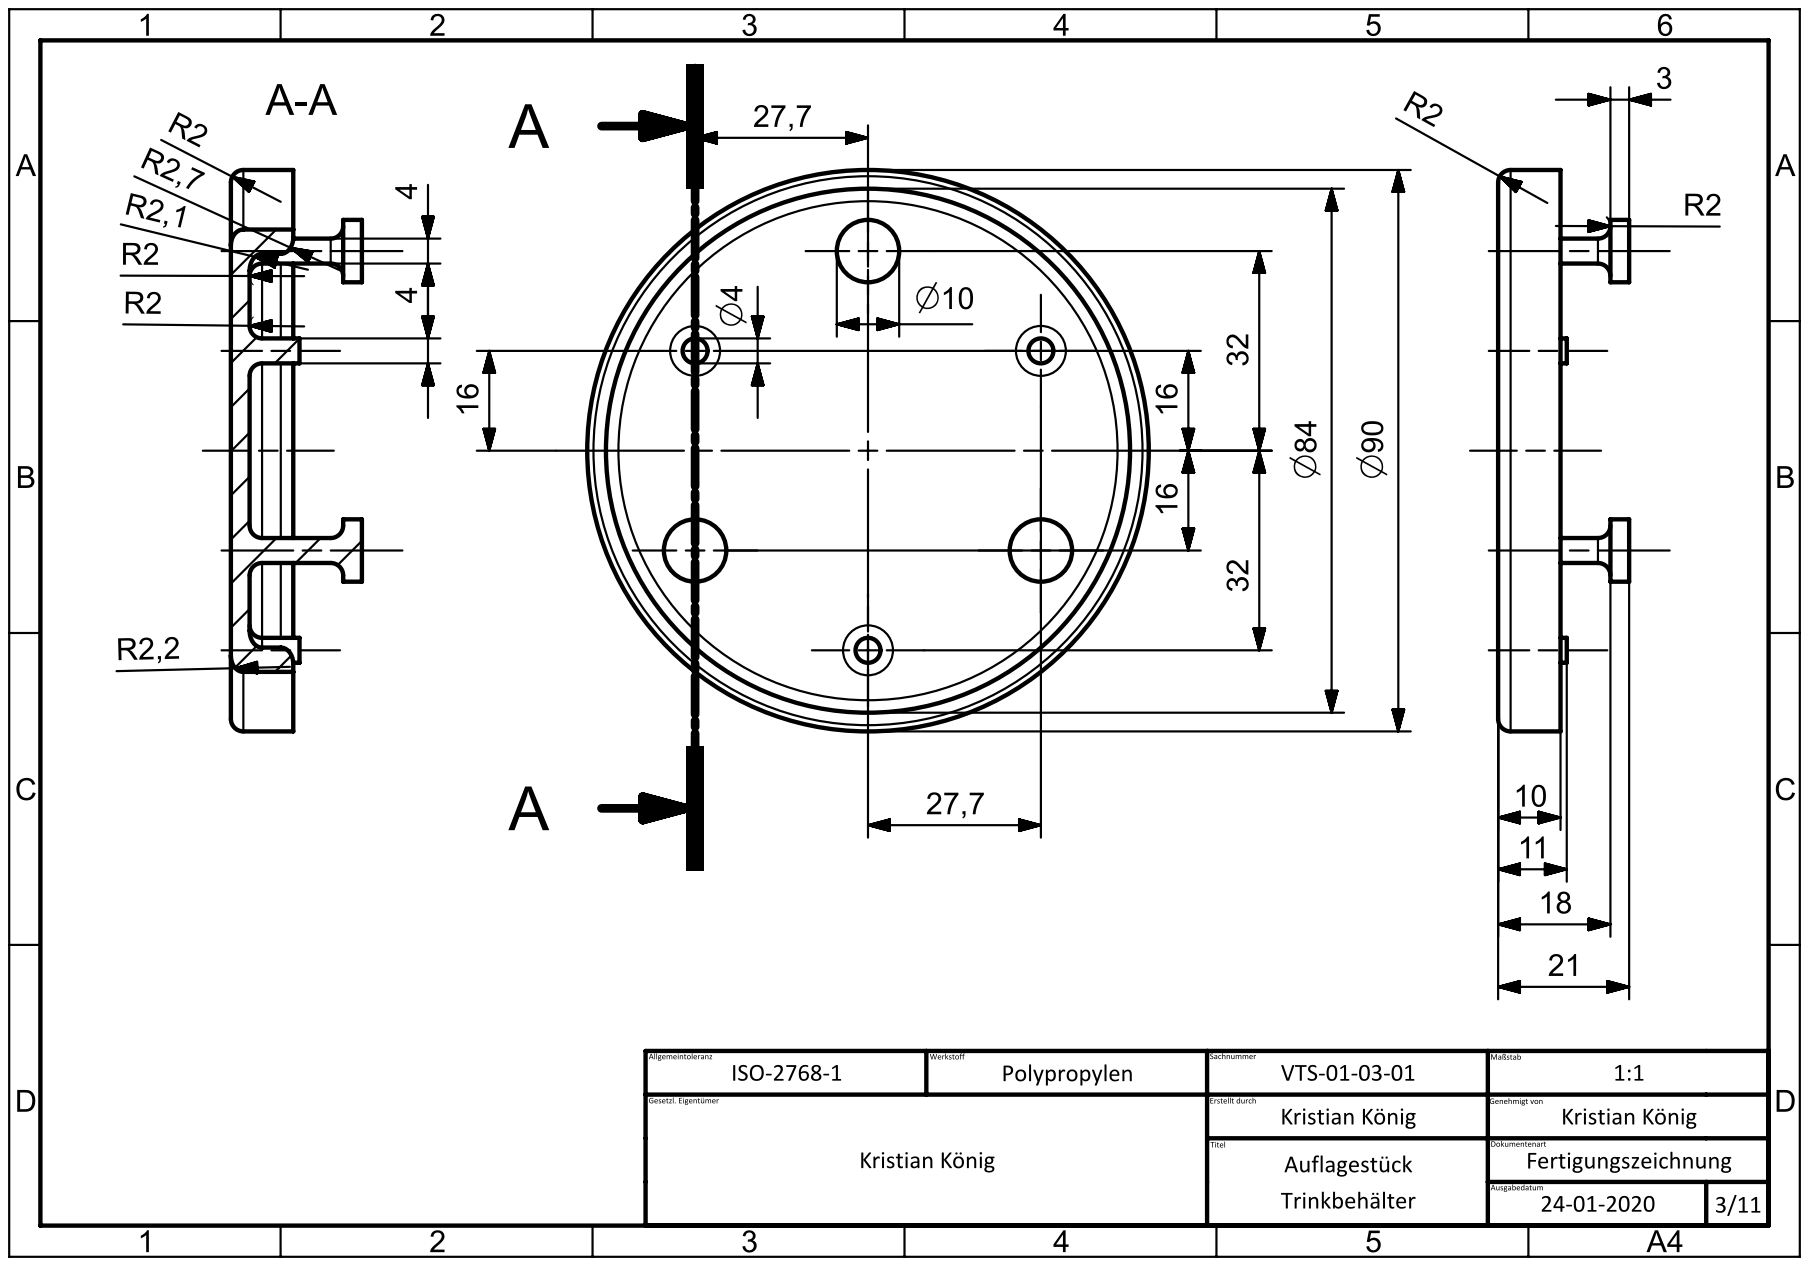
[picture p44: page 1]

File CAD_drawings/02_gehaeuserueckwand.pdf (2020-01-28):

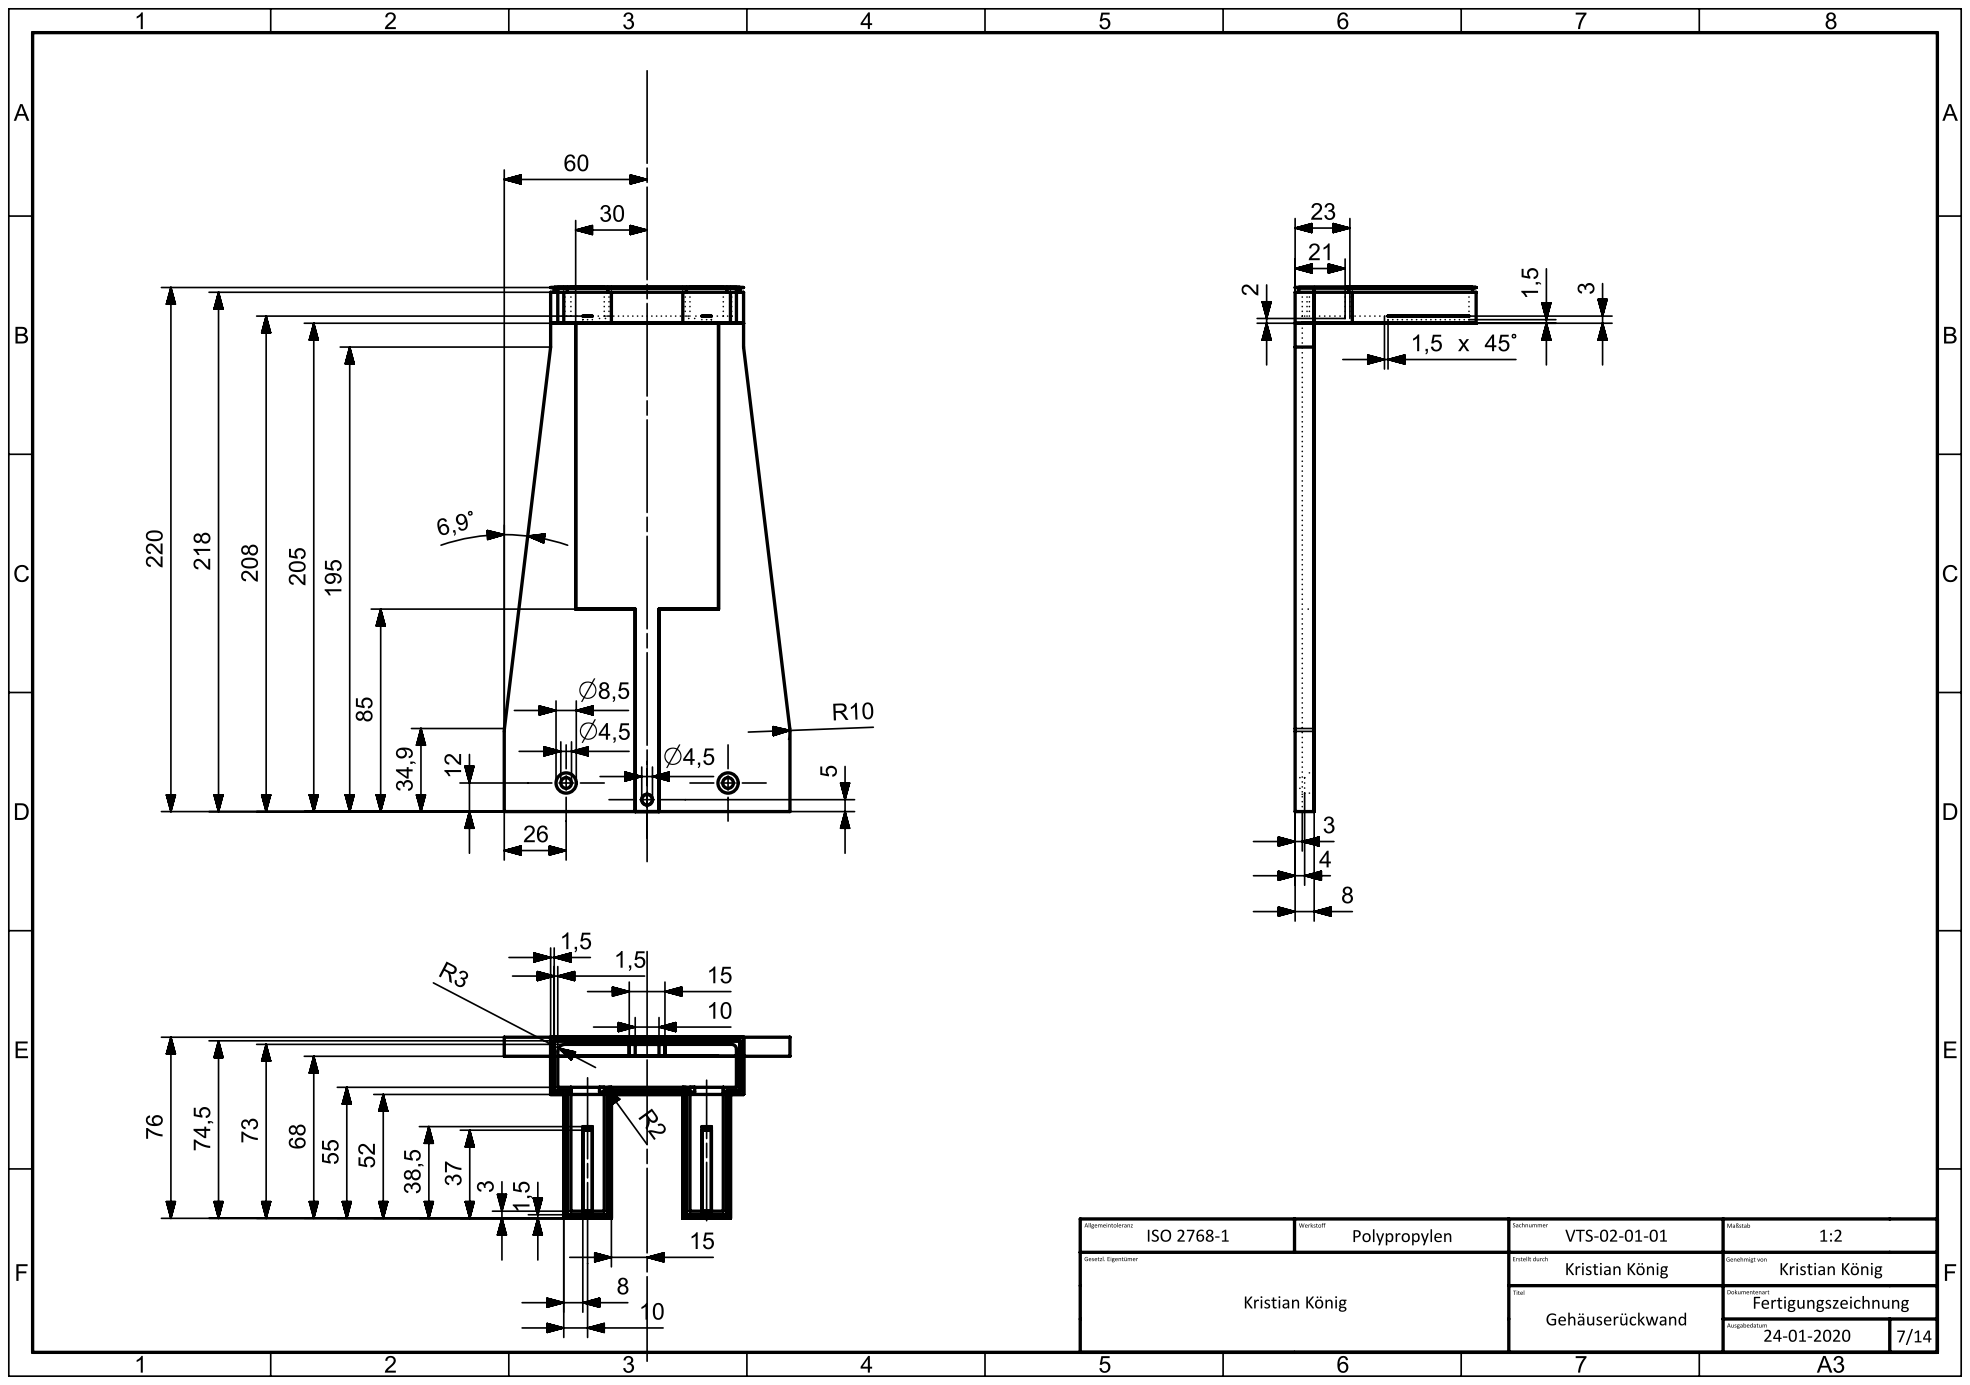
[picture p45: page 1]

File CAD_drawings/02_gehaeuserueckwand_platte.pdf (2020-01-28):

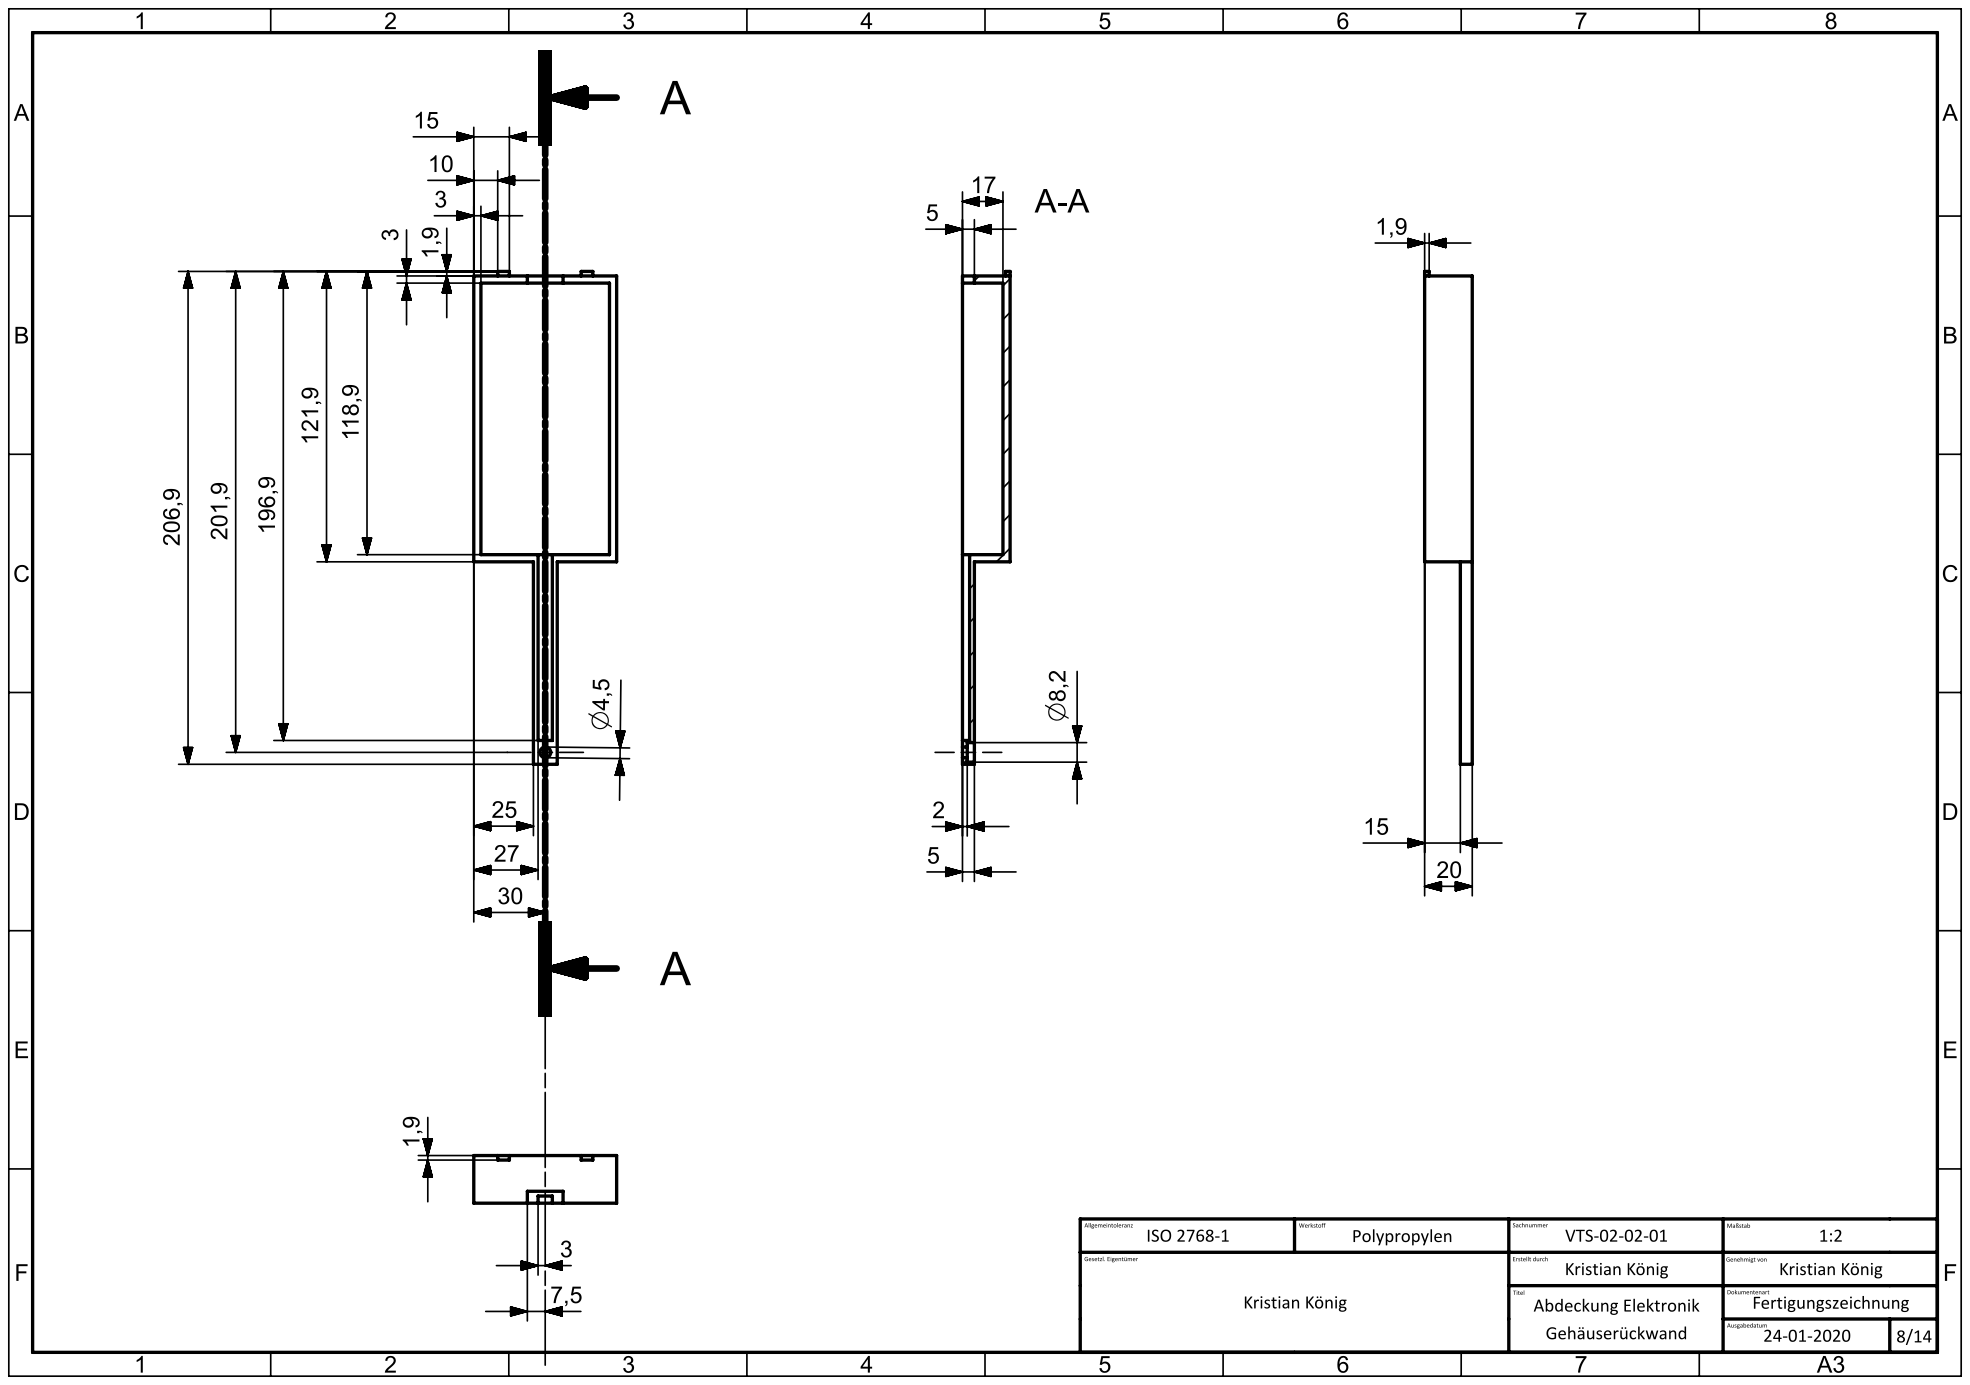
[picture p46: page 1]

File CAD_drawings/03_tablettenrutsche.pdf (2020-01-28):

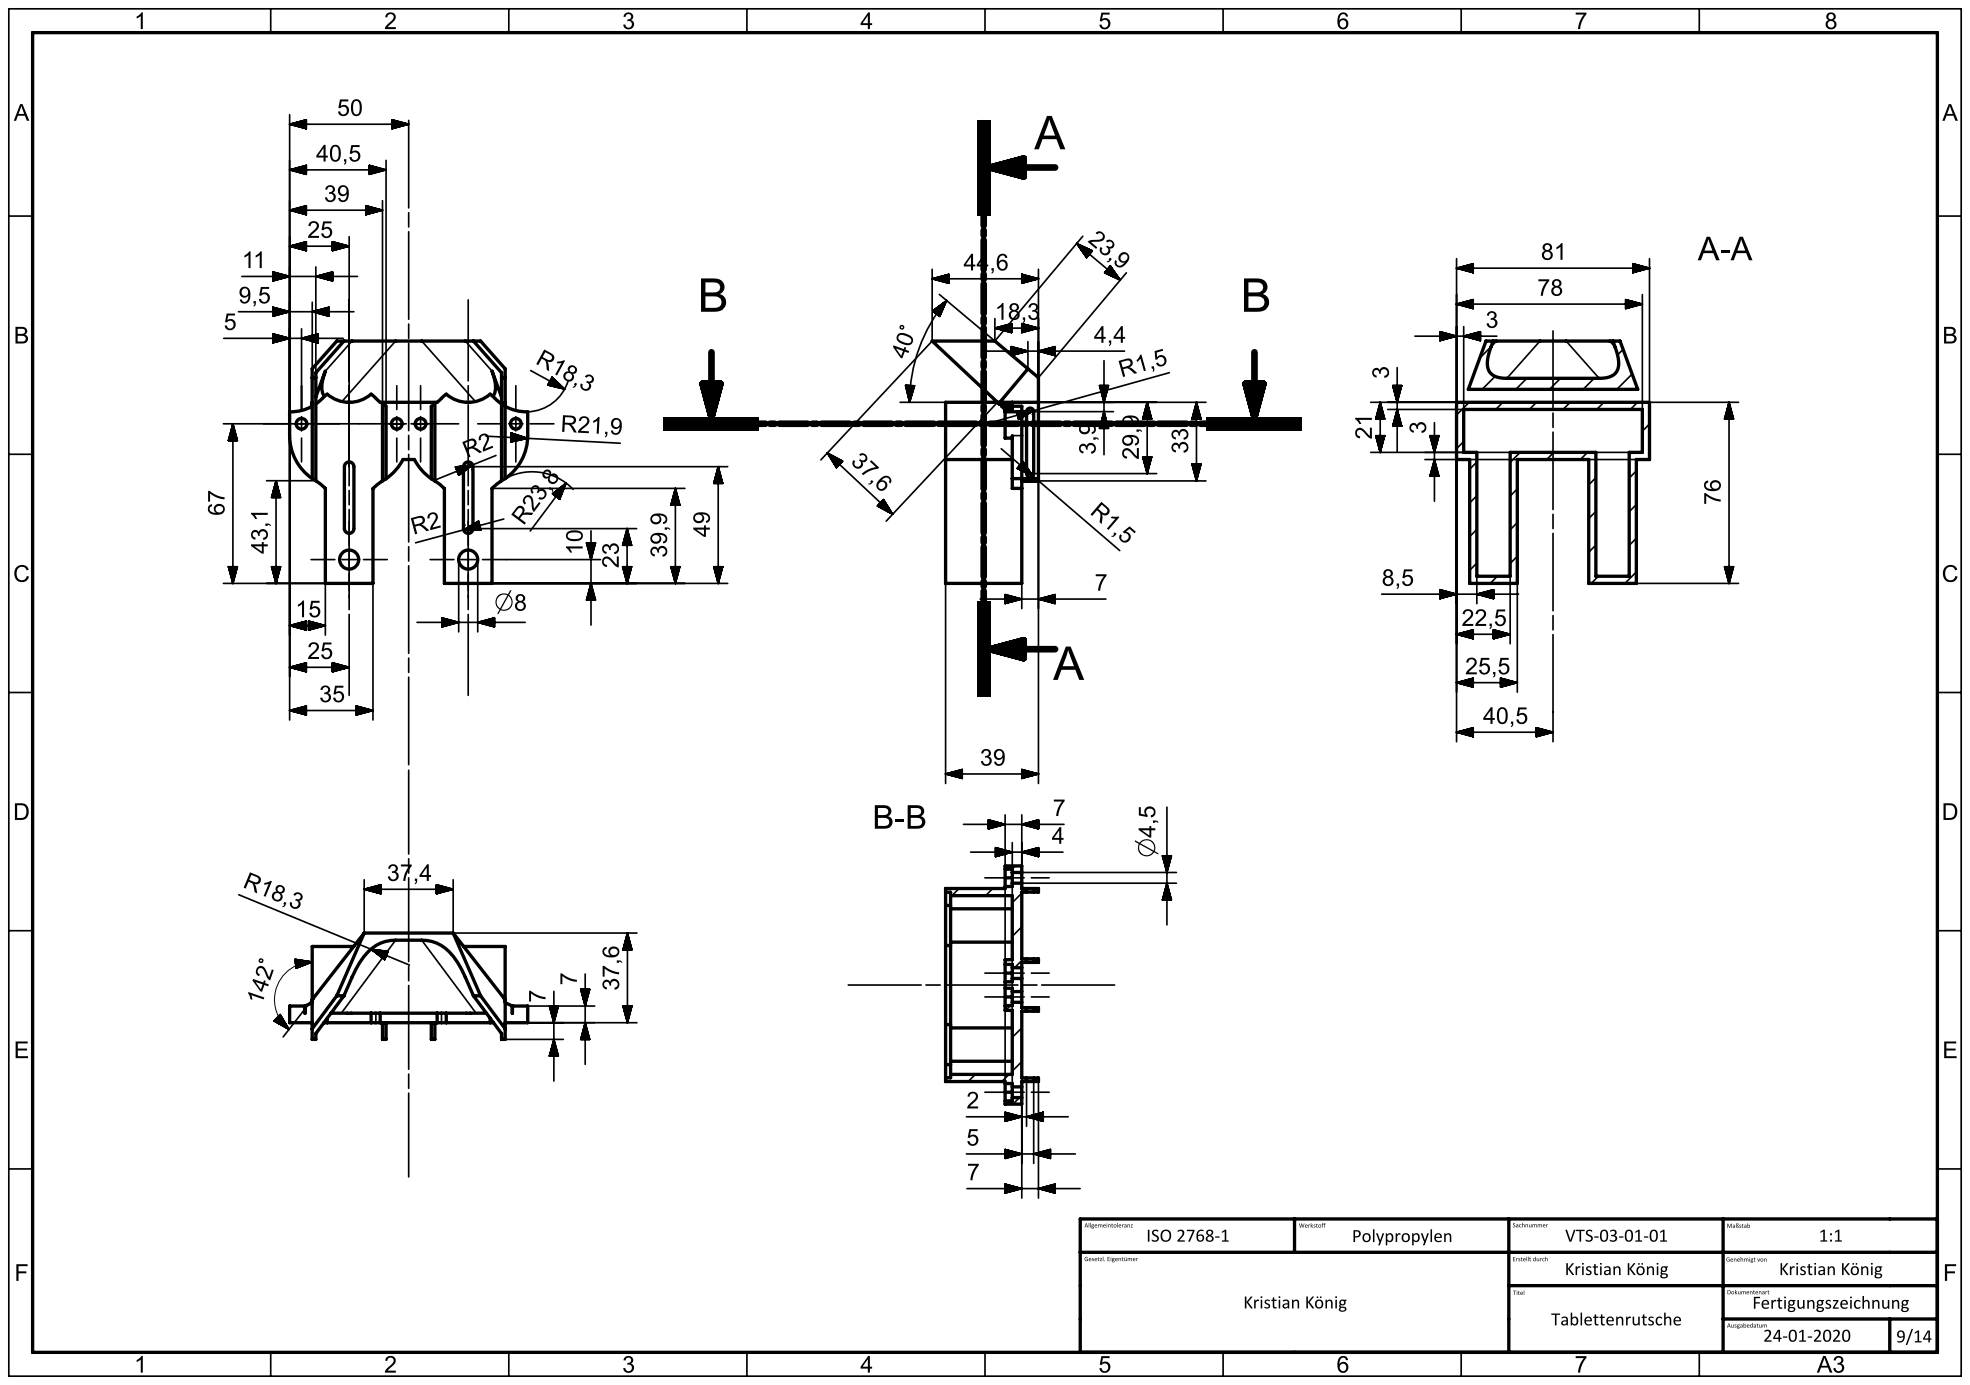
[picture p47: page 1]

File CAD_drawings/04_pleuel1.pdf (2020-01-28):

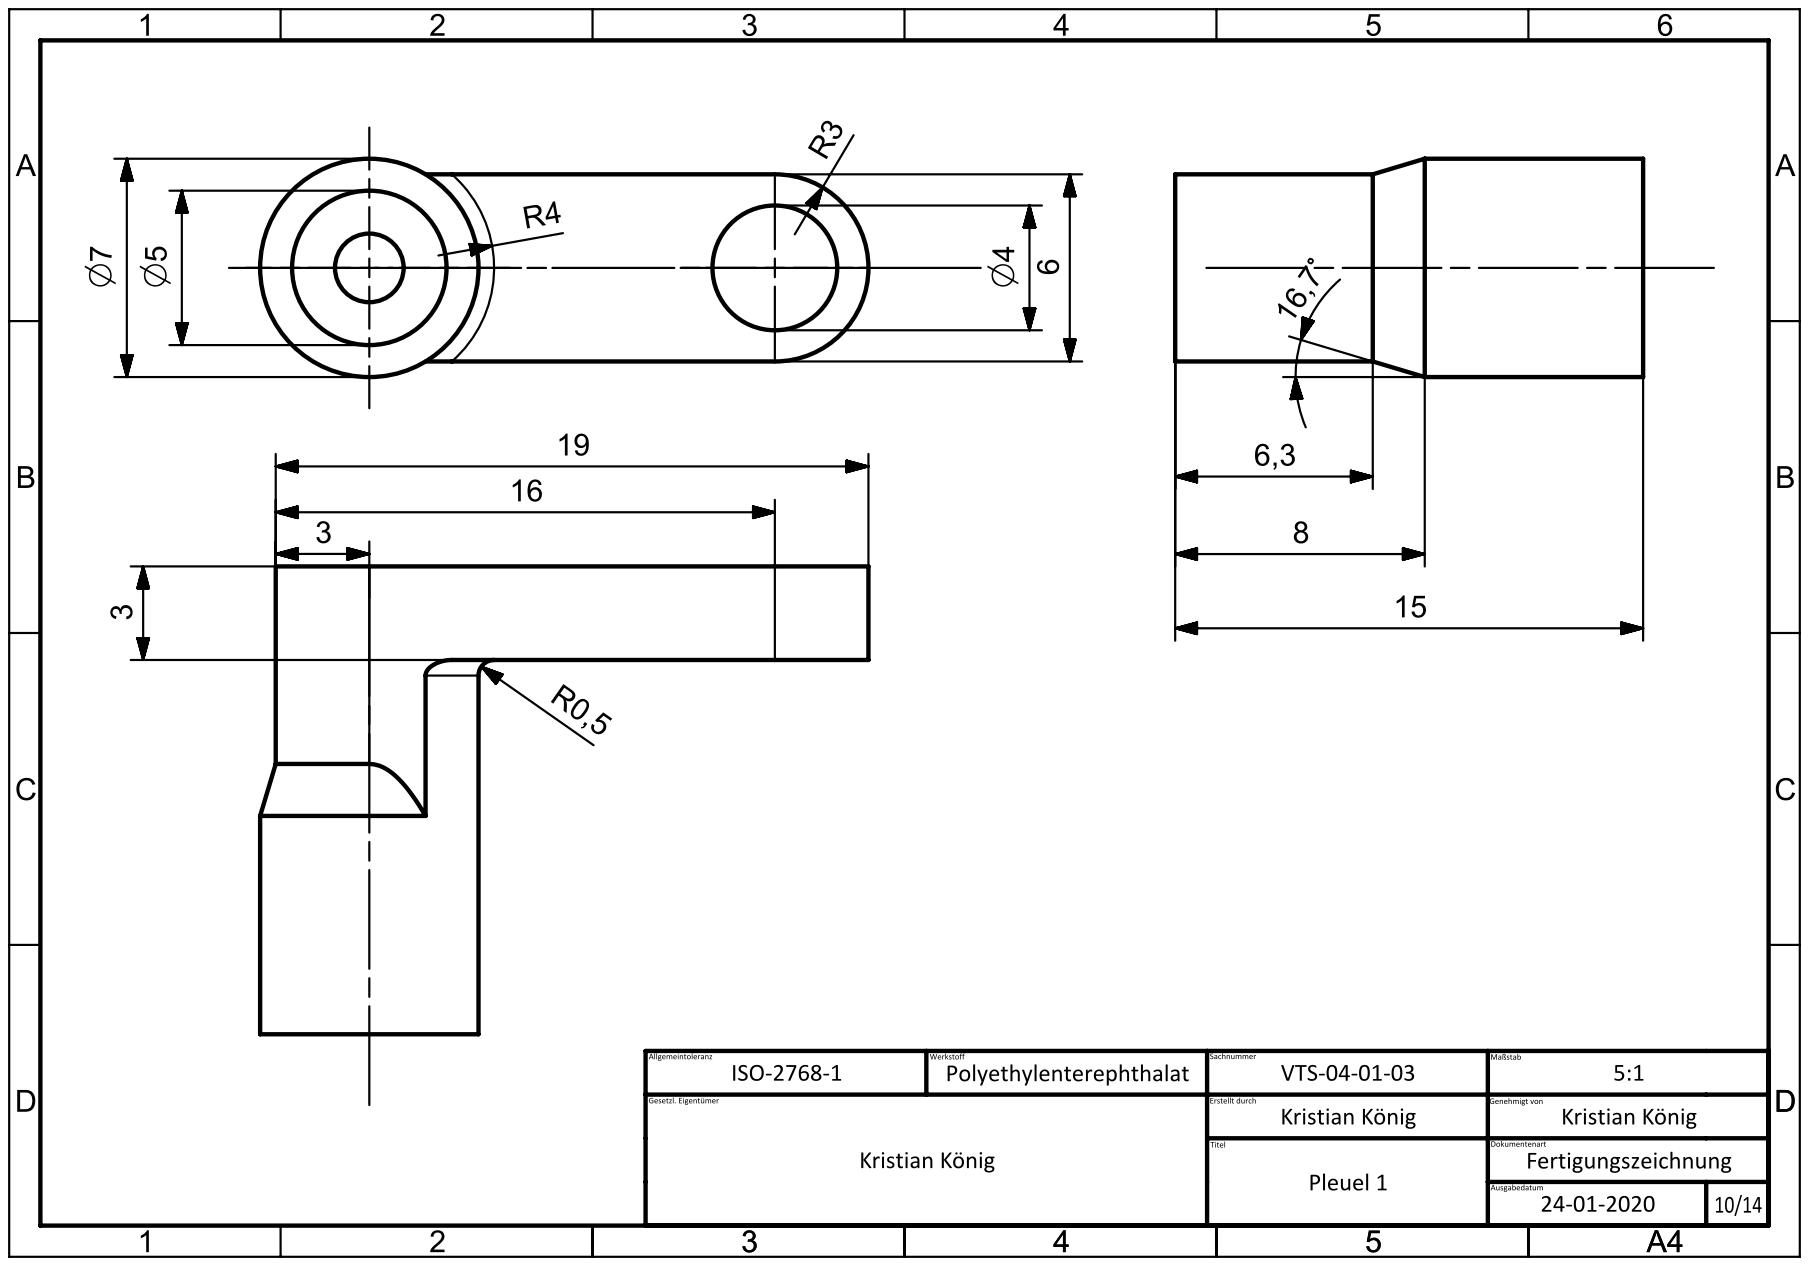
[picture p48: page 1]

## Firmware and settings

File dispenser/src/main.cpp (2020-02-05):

#include "main.hpp"

#define SCREEN_WIDTH 128 // OLED display width, in pixels
#define SCREEN_HEIGHT 32 // OLED display height, in pixels
#define SCREEN_ADDRESS 0x3C

Main::Main() {
	// SETTING UP RTC
	RTC->begin();

	if (not RTC->isrunning()) {
		Serial.println("ERROR: RTC is not running!");

		// stay stuck if no RTC is available
		while (true);
	}

	// CREATING CLASS INSTANCES
	this->buttonHandler = new ButtonHandler();
	this->displayHandler = new DisplayHandler();
	this->menuHandler = new MenuHandler();
	this->pillHandler = new PillHandler();

	// READING DATA FROM EEPROM
	uint16_t eeprom_index = 32;

	this->pillHandler->readData(&eeprom_index);

	// SET UP DISPLAY
	this->displayHandler->init(SCREEN_WIDTH, SCREEN_HEIGHT, SCREEN_ADDRESS);
	this->displayHandler->setMenu(
		this->menuHandler->menuOpenPtr(),
		this->menuHandler->menuIndexPtr(),
		this->menuHandler->menuOffsetPtr(),
		this->pillHandler
	);

	// GIVE MENU HANDLER ACCESS TO PILL DATA
	this->menuHandler->setObjectPointer(this->pillHandler);

	// REGISTERING MENU BUTTON CALLBACKS
	this->buttonHandler->addCallback(15, RISING, this->menuHandler, &MenuHandler::buttonPrev);
	this->buttonHandler->addCallback(14, RISING, this->menuHandler, &MenuHandler::buttonNext);
	this->buttonHandler->addCallback(16, RISING, this->menuHandler, &MenuHandler::buttonDown, 1000, 100);
	this->buttonHandler->addCallback(17, RISING, this->menuHandler, &MenuHandler::buttonUp, 1000, 100);

	this->buttonHandler->addCallback(18, RISING, this->pillHandler, &PillHandler::containerPlaced);

	// add a debug button to prepare a fake pill event
	this->buttonHandler->addCallback(19, RISING, this, &Main::prepareCustomPill);
};

Main::~Main() {
	delete this->buttonHandler;
	delete this->displayHandler;
	delete this->menuHandler;
	delete this->pillHandler;
}

bool Main::update() {
	this->displayHandler->update();
	this->buttonHandler->update();
	this->pillHandler->update();

	return true;
}

static void Main::prepareCustomPill(Main* self, uint8_t type) {
	Serial.println("Inserting fake pill event");
	self->pillHandler->createFakeTrigger();
}

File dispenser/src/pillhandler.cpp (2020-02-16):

#include "pillhandler.hpp"

PillStack::PillStack(uint8_t pin) {
	this->pin = pin;

	this->servo = new Servo();
	this->servo->attach(pin);

	this->retraction_time = 0;

	this->pill_ready = false;
}

PillStack::~PillStack() {

}

void PillStack::setPillAmountIndex(uint16_t index) {
	this->i_pill_amount = index;
}

void PillStack::setPillRefTimeIndex(uint16_t index) {
	this->i_pill_ref_time = index;
}

void PillStack::setPillIntervalIndex(uint16_t index) {
	this->i_pill_interval = index;
}

void PillStack::setPillAmount(uint8_t amount) {
	this->pill_amount = amount;

	// print debug information
	Serial.print("Setting Pill Amount at: ");
	Serial.println(this->pin);
	Serial.print("Amount: ");
	Serial.println(this->pill_amount);
	Serial.print("At storage position: ");
	Serial.println(this->i_pill_amount);
	Serial.println("----------------------------");
}

void PillStack::setPillRefTime(uint32_t time) {
	this->pill_ref_time = time;

	// print debug information
	DateTime time2(this->pill_ref_time);
	char buffer[40];
	sprintf(buffer, "%s - %02d:%02d:%02d", DAYS[time2.dayOfTheWeek()], time2.hour(), time2.minute(), time2.second());

	Serial.print("Setting Reference Time at: ");
	Serial.println(this->pin);
	Serial.print("Time: ");
	Serial.println(buffer);
	Serial.print("At storage position: ");
	Serial.println(this->i_pill_ref_time);
	Serial.println("----------------------------");
}

void PillStack::setPillInterval(uint32_t time) {
	this->pill_interval = time;

	// print debug information
	Serial.print("Setting Pill Interval at: ");
	Serial.println(this->pin);
	Serial.print("Time: ");
	Serial.println(this->pill_interval);
	Serial.print("At storage position: ");
	Serial.println(this->i_pill_interval);
	Serial.println("----------------------------");
}

uint8_t PillStack::getPillAmount() {
	return this->pill_amount;
}

uint32_t PillStack::getPillRefTime() {
	return this->pill_ref_time;
}

uint32_t PillStack::getPillInterval() {
	return this->pill_interval;
}

bool PillStack::isPillReady() {
	return pill_ready;
}

void PillStack::update() {
	// get current time
	DateTime time = RTC->now();

	if (not this->pill_ready and time.unixtime() >= this->pill_ref_time) {
		this->pill_ready = true;

		// start beeper
		tone(5, 1000, 750);

		// print debug information
		Serial.print("Pill is ready at pin: ");
		Serial.println(this->pin);
		Serial.println("----------------------------");
	}

	if (millis() > this->retraction_time) {
		this->servo->write(POS_PILL_IN);
	} else {
		this->servo->write(POS_PILL_OUT);
	}
}

void PillStack::throwPill() {
	if (this->pill_amount == 0) {
		// start beeper
		tone(5, 500, 350);

		return;
	}

	// set throw position time flag
	this->retraction_time = millis() + THROW_TIME;

	// set new time for next pill
	this->pill_ref_time += this->pill_interval;

	// decrease pill amount
	this->pill_amount -= 1;

	// pill is no longer ready
	this->pill_ready = false;

	// update EEPROM storage

	// we have to cache the index variables here since writeUint modifies it
	uint16_t i_pill_amount_ = this->i_pill_amount;
	uint16_t i_pill_ref_time_ = this->i_pill_ref_time;

	EEPROMW->writeUInt8(&i_pill_amount_, this->pill_amount);
	EEPROMW->writeUInt32(&i_pill_ref_time_, this->pill_ref_time);

	// print debug info
	DateTime time(this->pill_ref_time);
	char buffer[40];
	sprintf(buffer, "%s - %02d:%02d:%02d", DAYS[time.dayOfTheWeek()], time.hour(), time.minute(), time.second());

	Serial.print("Pill is thrown at pin: ");
	Serial.println(this->pin);
	Serial.print("Next pill ref time: ");
	Serial.println(buffer);
	Serial.print("Leftover pills: ");
	Serial.println(this->pill_amount);
	Serial.println("----------------------------");
}

void PillStack::refillPills() {
	this->pill_amount = 20;

	// print debug info
	Serial.print("Pillstack is refilled at: ");
	Serial.println(this->pin);
	Serial.print("New pill amount: ");
	Serial.println(this->pill_amount);
	Serial.println("----------------------------");

	// update EEPROM storage

	// we have to cache the index variables here since writeUint modifies it
	uint16_t i_pill_amount_ = this->i_pill_amount;

	EEPROMW->writeUInt32(&i_pill_amount_, this->pill_amount);
}

void PillStack::reset() {
	Serial.println("RESETTING DATA");

	// we have to cache the index variables here since writeUint modifies it
	uint16_t i_pill_amount_ = this->i_pill_amount;
	uint16_t pill_interval_ = this->pill_interval;
	uint16_t i_pill_ref_time_ = this->pill_ref_time;

	uint8_t new_pill_amount = 20;
	uint32_t new_pill_interval = 86400;

	DateTime time = RTC->now();

	uint32_t new_pill_ref_time = time.unixtime();

	EEPROMW->writeUInt32(&i_pill_amount_, new_pill_amount);
	EEPROMW->writeUInt32(&pill_interval_, new_pill_interval);
	EEPROMW->writeUInt32(&i_pill_ref_time_, new_pill_ref_time);

	this->setPillAmount(new_pill_amount);
	this->setPillInterval(new_pill_interval);
	this->setPillRefTime(new_pill_ref_time);
}

void PillStack::createFakeTrigger() {
	Serial.print("Creating fake trigger event at pin: ");
	Serial.println(this->pin);
	Serial.println("----------------------------");

	// get current time
	DateTime time = RTC->now();

	// create a fake pill ready event in 15 seconds
	this->pill_ref_time = time.unixtime() + 10;

	// update EEPROM storage

	// we have to cache the index variables here since writeUint modifies it
	uint16_t i_pill_ref_time_ = this->i_pill_ref_time;

	EEPROMW->writeUInt32(&i_pill_ref_time_, this->pill_ref_time);
}

PillHandler::PillHandler() {
	this->data_index = 0;

	this->pillStack[0] = new PillStack(7);
	this->pillStack[1] = new PillStack(6);

	this->container_placed = false;
}

PillHandler::~PillHandler() {
	
}

void PillHandler::createFakeTrigger() {
	// create a fake trigger for one of the both pillStacks
	this->pillStack[random(0, 2)]->createFakeTrigger();
}

void PillHandler::readData(uint16_t* index) {
	Serial.println("----------------------------");

	// cache storage position for later data update
	this->data_index = *index;

	// PILL HOLDER A
	this->pillStack[0]->setPillAmountIndex(*index);
	this->pillStack[0]->setPillAmount(EEPROMW->readUInt8(index));

	this->pillStack[0]->setPillRefTimeIndex(*index);
	this->pillStack[0]->setPillRefTime(EEPROMW->readUInt32(index));

	this->pillStack[0]->setPillIntervalIndex(*index);
	this->pillStack[0]->setPillInterval(EEPROMW->readUInt32(index));

	// PILL HOLDER B
	this->pillStack[1]->setPillAmountIndex(*index);
	this->pillStack[1]->setPillAmount(EEPROMW->readUInt8(index));

	this->pillStack[1]->setPillRefTimeIndex(*index);
	this->pillStack[1]->setPillRefTime(EEPROMW->readUInt32(index));

	this->pillStack[1]->setPillIntervalIndex(*index);
	this->pillStack[1]->setPillInterval(EEPROMW->readUInt32(index));
}

void PillHandler::update() {
	this->pillStack[0]->update();
	this->pillStack[1]->update();
}
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

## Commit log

2019-11-25 gantt plan
    [ganttplan.xlsx]
2019-11-28 lösprinzipirn
    [ganttplan.xlsx, konsistenz.xlsx, loeskomb.xlsx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]
2019-11-28 added bw schematic
2019-12-06 added docs and button handler
2019-12-10 removed debug prints
2019-12-23 03 ashby
    [Gehaeuseboden.prt]
2020-01-06 cad pt2
    [Gehaeuseboden.prt, fuellstandtaster.prt, gehaeuserueckwand.prt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]
2020-01-23 change to arduino mega
2020-01-28 cad delete
    [Gehaeuseboden.prt, fuellstandtaster.prt, gehaeuserueckwand.prt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]
2020-01-28 cad modelling and drawing
    [00_vitamintablettenspender_zusammenbau.prt, 00_vitamintablettenspender_zusammenbau_dimetrisch.prt, 01_gehaeuseboden.prt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]
2020-01-28 current pill values are now stored
2020-01-29 implement buzzer and pill timing
    [main.cpp, pillhandler.cpp]
2020-02-15 finishing and fixing pillhandling
    [eeprom.cpp, pillhandler.cpp]
